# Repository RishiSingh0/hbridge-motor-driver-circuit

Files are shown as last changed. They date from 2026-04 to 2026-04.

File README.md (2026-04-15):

# H-Bridge Motor Driver

This is the motor driver for **Robo Maestro**, a piano-playing robot I built with my team for ELEC 391 (2025W2). It lives on its own daughter board and drives a geared DC motor that slides the robot's hand left and right along the keyboard. A PID loop running on an STM32F446 on the [piano-robot-motherboard](https://github.com/RishiSingh0/piano-robot-motherboard) closes the position loop over this board.

The short version: I designed it, it passed the half-way demo on a bench DC signal, and the first time the control team hit it with real PWM at 10 kHz the MOSFETs started cooking within seconds. The boards were already fabricated, so the fix had to happen on the physical board I already had. The reworked board ran the full song at 20 kHz PWM in the final demo.

---

## The task

My job on the hardware side was an H-bridge the MCU could control to move the robot laterally along the piano. CW would push it right along the keyboard, CCW would push it left, and the PID loop would throw PWM at whichever direction pin it wanted active.

## The board I designed

The design split the MCU side from the motor's HV+ rail and used optocouplers to bridge the two. The MCU sat on the low-voltage 3.3 V side and drove the opto LEDs on the CW and CCW lines; the opto outputs on the HV side did the actual gate drive.

Here are the schematic and layout I sent off to JLCPCB:

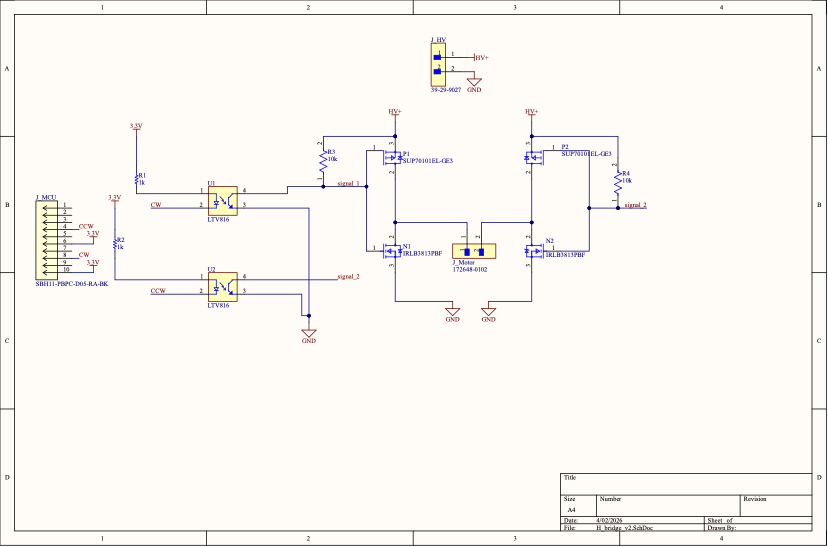
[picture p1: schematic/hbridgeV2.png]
H-Bridge v2 schematic, original as-fabricated design with shared-gate optocoupler drive


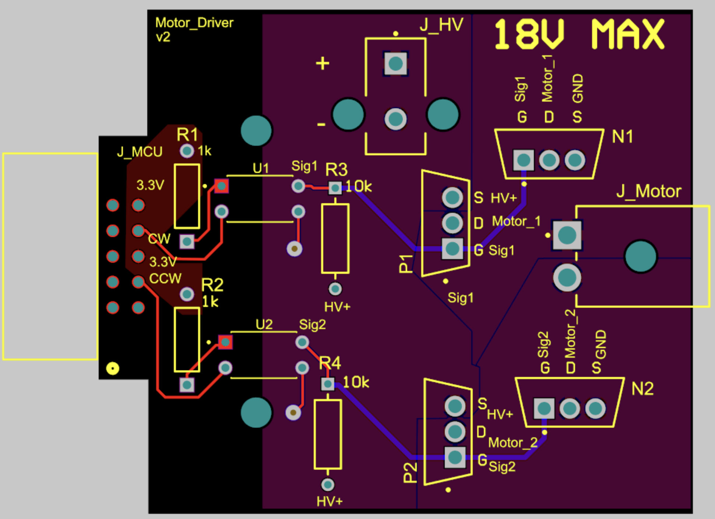
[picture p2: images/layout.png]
H-Bridge v2 PCB layout, top view of the fabricated board with J_MCU connector on the left, the two LTV816 optocouplers driving the gate traces, and two half-bridges feeding the motor connector on the right


One GPIO per leg, through an LTV816 optocoupler, driving **both** the high-side PMOS (SUP70101EL-GE3) and the low-side NMOS (IRLB3813PBF) from the same gate trace. PMOS and NMOS are naturally complementary, so in theory one signal is enough: take the trace high, NMOS on and PMOS off; take it low, PMOS on and NMOS off. Two legs, two opto lines, done. HV+ rail 12–16 V, motor stall 8.5 A, motor connector in the middle.

## The half-way demo passed

For the half-way demo I brought the board up against a bench power supply and tested it the simplest way you can test an H-bridge: hold CW at a 3.3 V DC level on the optocoupler input and watch the motor spin right, then drop CW, assert CCW, and watch it spin left. Motor spun both ways, nothing got hot, and I moved on to integration. (Note: during PID integration the firmware's CW/CCW labels were later swapped, so the final RoboMaestro `MotorCW` drives the opposite physical direction from what this paragraph calls "right".)

A DC command only transitions once, when you change direction, and a single transition is too brief to cause meaningful heating even if shoot-through is happening on it. The bench test was only checking the steady states on either side of the transition, not the transition itself.

## PWM came in during integration and immediately started frying FETs

During integration, the STM32 started driving the H-bridge's CW and CCW inputs with 10 kHz PWM from TIM1 (channels 1 and 2 on PA8 and PA9). Within seconds the MOSFETs started running hot and burning out.

Because the board had worked at the half-way demo, my first instinct was that something on the software side had gone wrong. Nothing in the hardware had changed, and the only new variable was the waveform coming out of the STM32, so I spent a while digging into the firmware (PWM setup, timer channels, the duty cycle path) and got nowhere. Nothing on the software side actually looked broken. In the meantime we dropped the PWM frequency way down just to see what would happen. The FETs still got hot, just much more slowly, which was itself a clue: whatever was cooking them was happening per switching edge, not per steady-state cycle, so it was pointing at something that scaled with transition rate rather than at a software bug.

So I pivoted back to hardware. I searched for why MOSFETs might run hot under PWM and found articles on **shoot-through current** in H-bridges caused by MOSFET transition times. The idea: if both FETs in a half-bridge are even momentarily on at the same time, there's a dead short from HV+ to GND, and if that happens on every PWM edge you're shorting the supply thousands of times a second. I took that to the scope.

## Confirming it on the scope

I put a Tektronix scope on one half-bridge leg and looked at VGS on both FETs simultaneously:

- Low-side (NMOS): probe directly on the gate, since the source is at GND.
- High-side (PMOS): math channel `CH1 − CH2`, with CH1 on the PMOS gate and CH2 on its source at HV+. You need the difference because the PMOS source floats at HV+, not GND.

Then I fed PWM in and froze the scope on a transition edge:

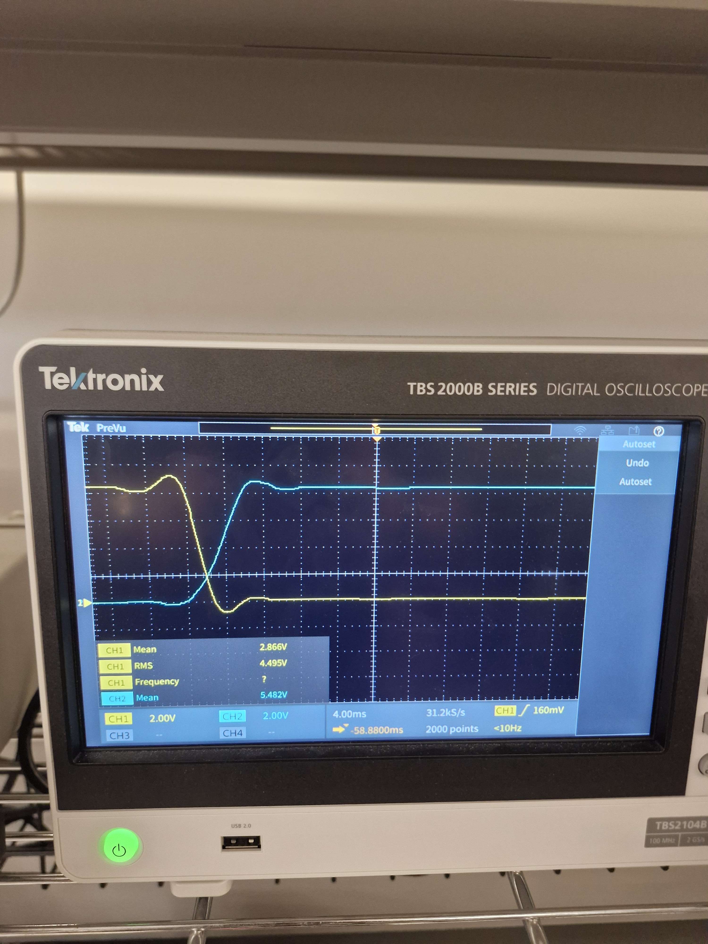
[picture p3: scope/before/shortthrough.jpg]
Scope trace before the rework: both VGS traces transition at the same instant and cross through the mid-rail together, with an X-shaped overlap region where both FETs are partially conducting


Both traces X through each other in the middle of every edge. For the duration of that X, both FETs are sitting in their linear regions together and there's a low-resistance path from HV+ through both of them straight to GND. At 10 kHz that's happening on every single PWM edge, which works out to tens of thousands of near-shorts across the supply per second. Exactly what was cooking the FETs.

## Where the slow transition actually comes from

With the failure confirmed on the scope, I went back to the datasheets to work out why the transitions were so slow in the first place.

The LTV816 phototransistor output transition time alone is around 4 µs typical and up to 18 µs worst case. That's already a long edge. On top of that, the shared-gate node on each leg is loaded by both the PMOS and the NMOS input capacitance (Ciss), which for these power FETs is in the multi-nF range each. Call it somewhere around 10–15 nF total hanging off the 10 kΩ pull-up.

That gives an RC time constant somewhere around 100–150 µs, comparable to or longer than the 100 µs PWM period at 10 kHz. The gate can't finish its transition before the next one starts, so both FETs spend a huge fraction of every period sitting in their linear region at the same time. With these parts and this topology, there was no PWM duty cycle that would have actually worked at 10 kHz.

## The constraint I had to design around

The boards were already fabricated and populated. Whatever the fix was, it had to happen on this physical piece of FR4, not a respin.

## The idea I considered and dropped

My first instinct was to add some form of dead-time: either on the firmware side, or with passive components at the gates. I spent a bit of time on this before realising that if I could just give the MCU direct hardware control over when each PMOS is allowed to be on, I wouldn't need dead-time in the first place. The PMOS could only ever be on when the firmware explicitly said so, and the firmware would simply never allow both PMOSes on at once. Software dead-time also had a separate problem: it would have inserted delay into every PWM transition, which would have shown up as tempo drift in the piano playing since the PID is closing a position loop around a moving musical instrument. The hardware enable approach avoids both issues, and that's the direction I went.

## The fix: break the shared gate and give the MCU hardware enables

Instead of trying to shape the existing shared-gate drive, I decided to split it apart and give the MCU **independent** control of each PMOS. Here's the clean schematic of the post-rework topology:

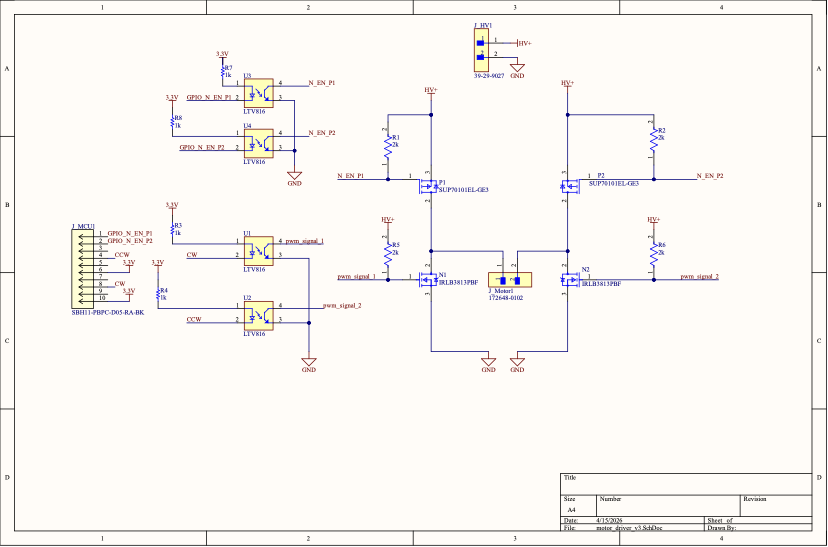
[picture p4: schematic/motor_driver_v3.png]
v3 schematic of the reworked H-bridge: original LTV816 optocouplers (U1, U2) driving only the NMOS gates through 2 kΩ pull-ups, plus two new LTV816 optocouplers (U3, U4) driven by dedicated GPIO enable signals and driving the PMOS gates through their own 2 kΩ pull-ups


And the handwritten planning sketch from when I was deciding what to cut and where to jump:

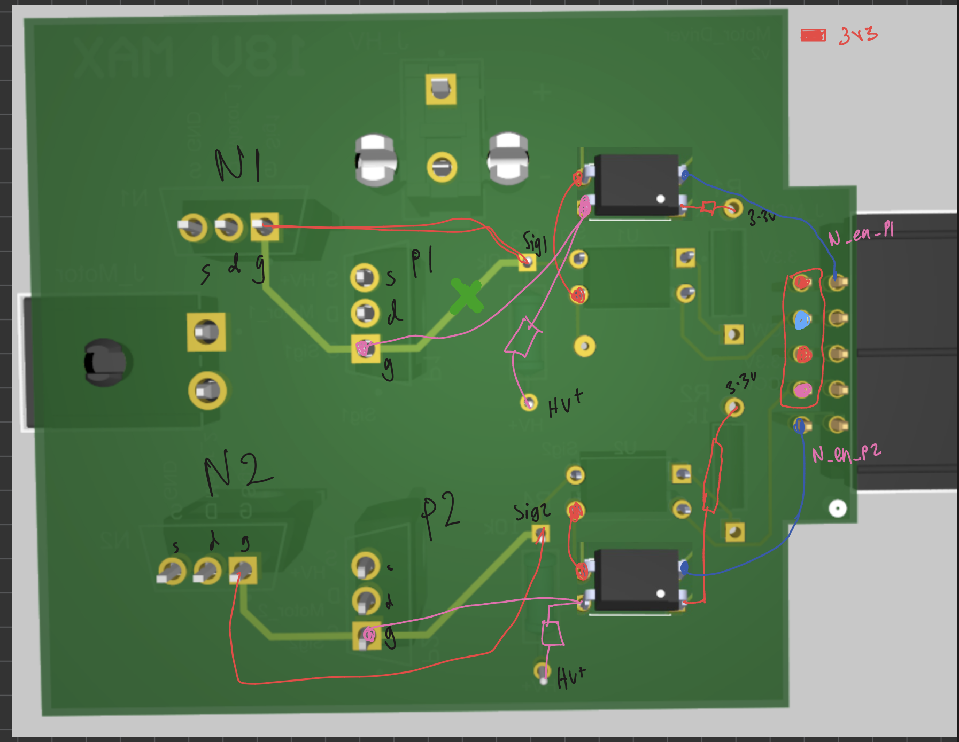
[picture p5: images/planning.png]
Handwritten planning sketch for the rework, showing which traces to cut and where to route the new enable signals


The new topology:

1. Cut 4 traces, two per leg (one on the gate-to-gate run between the NMOS and PMOS, one on the signal trace going into the PMOS gate). In hindsight one cut per leg would have been enough, just the signal-to-PMOS-gate trace, and the original front-side optocoupler could have kept driving the NMOS while the new back-side optos drove the isolated PMOS gates. But I did this rework between 1 and 4am and wasn't optimising for minimum cuts; I just wanted the PMOS gate completely off the shared node.
2. Desolder the original 10 kΩ pull-ups (R3, R4) and replace them with 2 kΩ. These resistors sit on the (now NMOS-only) shared node, and the smaller value drops the RC time constant enough for the NMOS gate to track 10+ kHz PWM without the transition-overlap problem.
3. Add 2 new STM32 GPIOs (PB5 and PB6) as dedicated PMOS enables, one per leg.
4. Add 2 new single-channel optocouplers driven by those GPIOs, wired to the now-isolated PMOS gates. Also solder in 2 more 2 kΩ resistors as pull-ups on the new optos' output side so the PMOS gates have a defined state when the enable signal is idle.

The two new optos were soldered **directly onto the back of the existing PCB**. The original LTV816s were through-hole parts, so their pins were already exposed on the back side and I could tap into them with bodge wires. No extra perfboard, no sub-board, just two optos and some wire on the back of the existing board.

Here's what the rework looked like from behind:

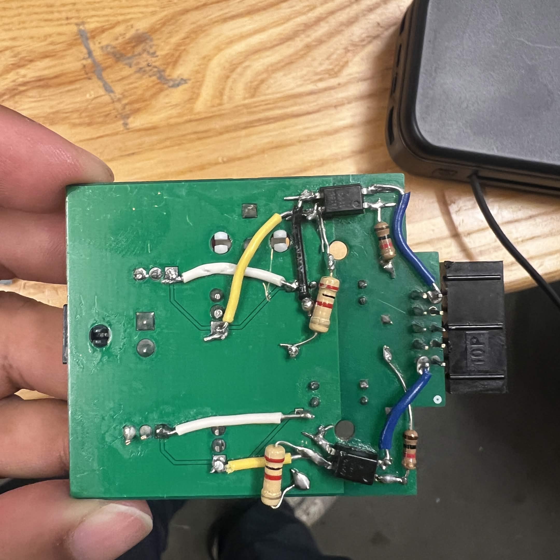
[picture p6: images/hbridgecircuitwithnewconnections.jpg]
Back side of the H-bridge PCB with two single-channel optocouplers and bodge wires soldered on, implementing the enable-signal rework


And the new enable signal lines being tapped into on the motherboard side:

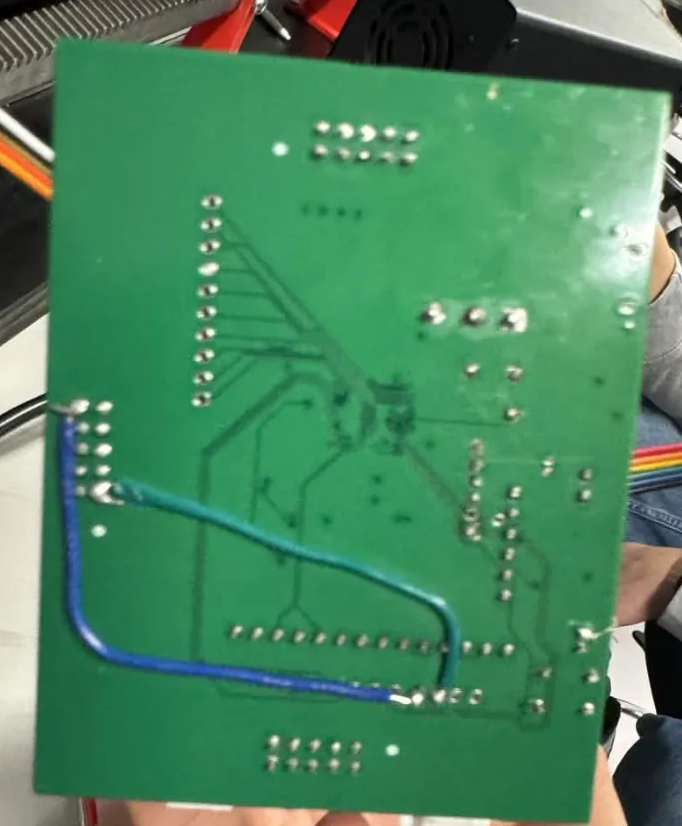
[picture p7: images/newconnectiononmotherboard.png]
New enable signal wires soldered onto the back of the motherboard, connecting two STM32 GPIOs out to the H-bridge daughter board's added optocouplers


And reinstalled in the stack:

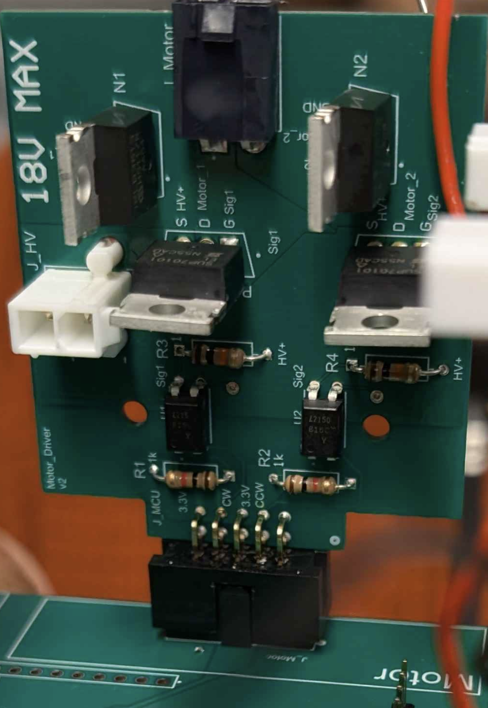
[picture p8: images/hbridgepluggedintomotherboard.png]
Reworked H-bridge daughter board plugged back into the motherboard stack


After the rework, the total signal count into the H-bridge was 4 GPIOs: 2 PWM lines to the NMOSes (unchanged from the original), plus 2 enable lines to the new PMOS-drive optos. The firmware-side logic, written in terms of the actual MCU pin voltages, collapses into a small table:

| State | EN1 | EN2 | N1 | N2 |
|---|---|---|---|---|
| Idle / coast | 3.3V | 3.3V | 0V | 0V |
| Drive CW | 0V | 3.3V | 0V | PWM |
| Drive CCW | 3.3V | 0V | PWM | 0V |

`EN1`/`EN2` are **active-low** through the opto (0V → LED lit → BJT on → PMOS gate pulled low → P ON). `N1`/`N2` are **non-inverting** overall (3.3V → N ON, 0V → N OFF), so "PWM" in the table means the pin is pulsed between 0V and 3.3V and the NMOS follows directly. CW drives diagonally through P1 + N2; CCW drives diagonally through P2 + N1.

On any CW↔CCW transition, the firmware first drives both EN pins to 3.3V (both PMOSes off) before asserting the opposite pair. No overlap is possible, because the PMOSes can only be ON when the MCU explicitly pulls an EN pin low, and the firmware never pulls both EN pins low simultaneously.

The two new optos don't need to be fast either. They're not in the PWM path. They only switch at direction changes, which happen orders of magnitude slower than the PWM frequency, so their multi-µs transition times don't matter.

## After the rework

Back on the scope, same probe setup as before:

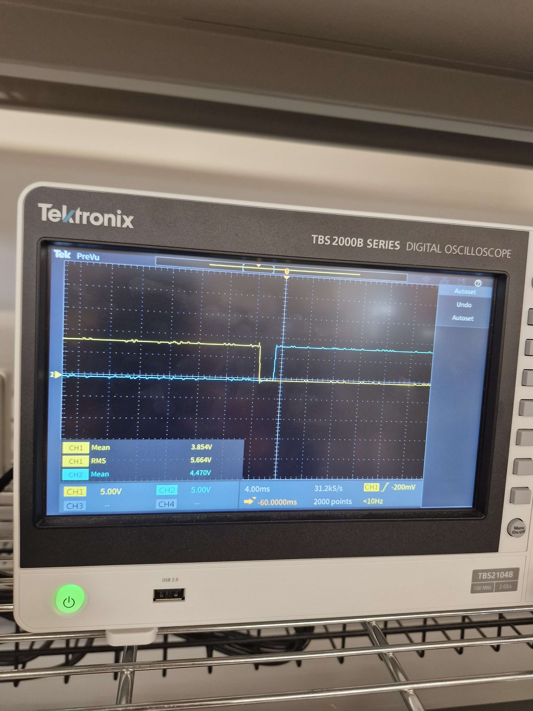
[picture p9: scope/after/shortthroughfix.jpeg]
Scope trace after the rework: one VGS goes fully to its off state before the other asserts on, with a clear horizontal gap between the two edges


Clean non-overlap. One FET is fully off before the other turns on, and there's a clear horizontal gap where neither FET is conducting. No overlap, no shoot-through, no low-resistance path. Same behaviour on both the rising and the falling edge of the switching cycle.

I brought the PWM back up to 10 kHz, then pushed it to **20 kHz for the final demo performance**. The FETs stayed cool at both frequencies, and the robot played the full song end-to-end on the reworked board.

## What I'd do differently

1. **PWM has to be in the very first integration test.** Shoot-through only shows up during a transition, so a DC bench bring-up is structurally incapable of catching it. If you wait until PID integration to introduce PWM, the first time you see the failure is also the first time you're losing FETs.
2. **Don't roll complementary MOSFET drive from a generic optocoupler.** LTV816 transition times (up to 18 µs) are more than an order of magnitude slower than the sub-microsecond edges you need at 10–20 kHz. If I respin this board, I'm using a dedicated half-bridge gate driver IC (IR2184 / IR2110 or similar) with built-in dead-time, or driving each gate independently from the start and adding firmware dead-time explicitly.

---

## Files in this repo

- [`schematic/hbridgeV2.pdf`](schematic/hbridgeV2.pdf): the as-fabricated v2 schematic shown at the top of this README (rendered PNG next to the PDF)
- [`schematic/motor_driver_v3.pdf`](schematic/motor_driver_v3.pdf): the post-rework v3 schematic shown in the fix section (rendered PNG next to the PDF)
- [`hardware/`](hardware): Altium source for the fabricated v2 design (schematic, PCB, BOM, project file)
- [`scope/before/`](scope/before) and [`scope/after/`](scope/after): scope captures of VGS on one half-bridge leg before and after the rework
- [`images/`](images): planning sketch, original PCB layout, and photos of the bodged board
- [`notes.txt`](notes.txt): the raw notes I wrote while figuring out the fix, preserved as-is

There's no v3 PCB layout planned; the final demo ran on the reworked v2.

## Related

- Main system repo: [piano-robot-motherboard](https://github.com/RishiSingh0/piano-robot-motherboard)
- Background reading that helped: [AllAboutCircuits: H-bridge dead-time and shoot-through](https://www.allaboutcircuits.com/technical-articles/h-bridge-dc-motor-control-complementary-pulse-width-modulation-pwm-shoot-through-dead-time-pwm/)

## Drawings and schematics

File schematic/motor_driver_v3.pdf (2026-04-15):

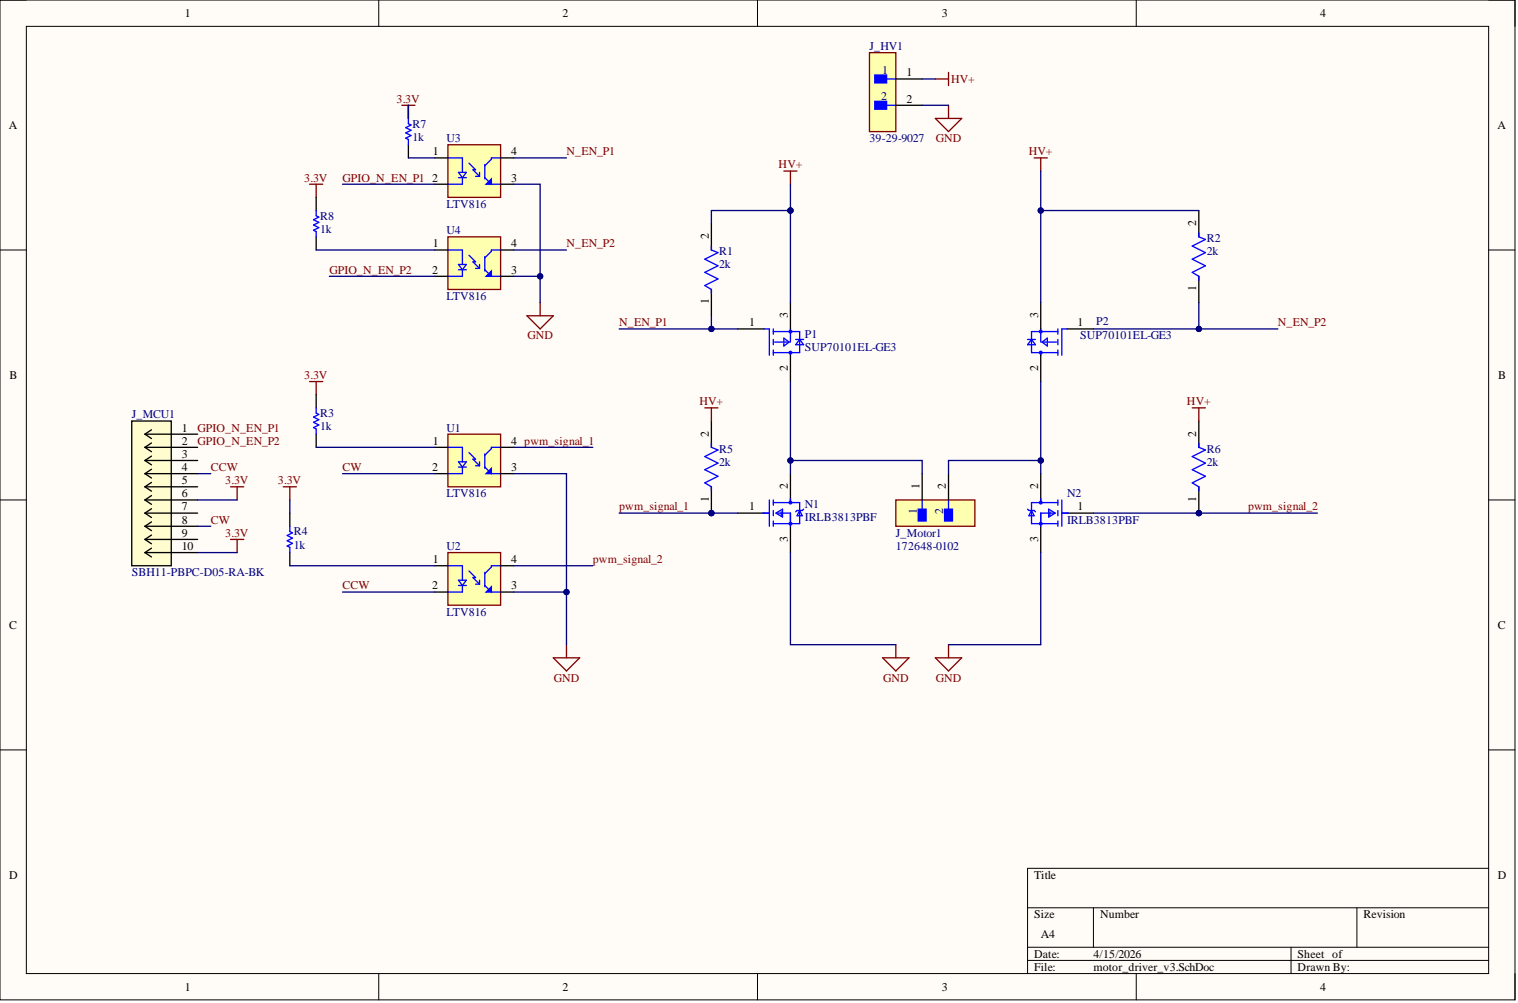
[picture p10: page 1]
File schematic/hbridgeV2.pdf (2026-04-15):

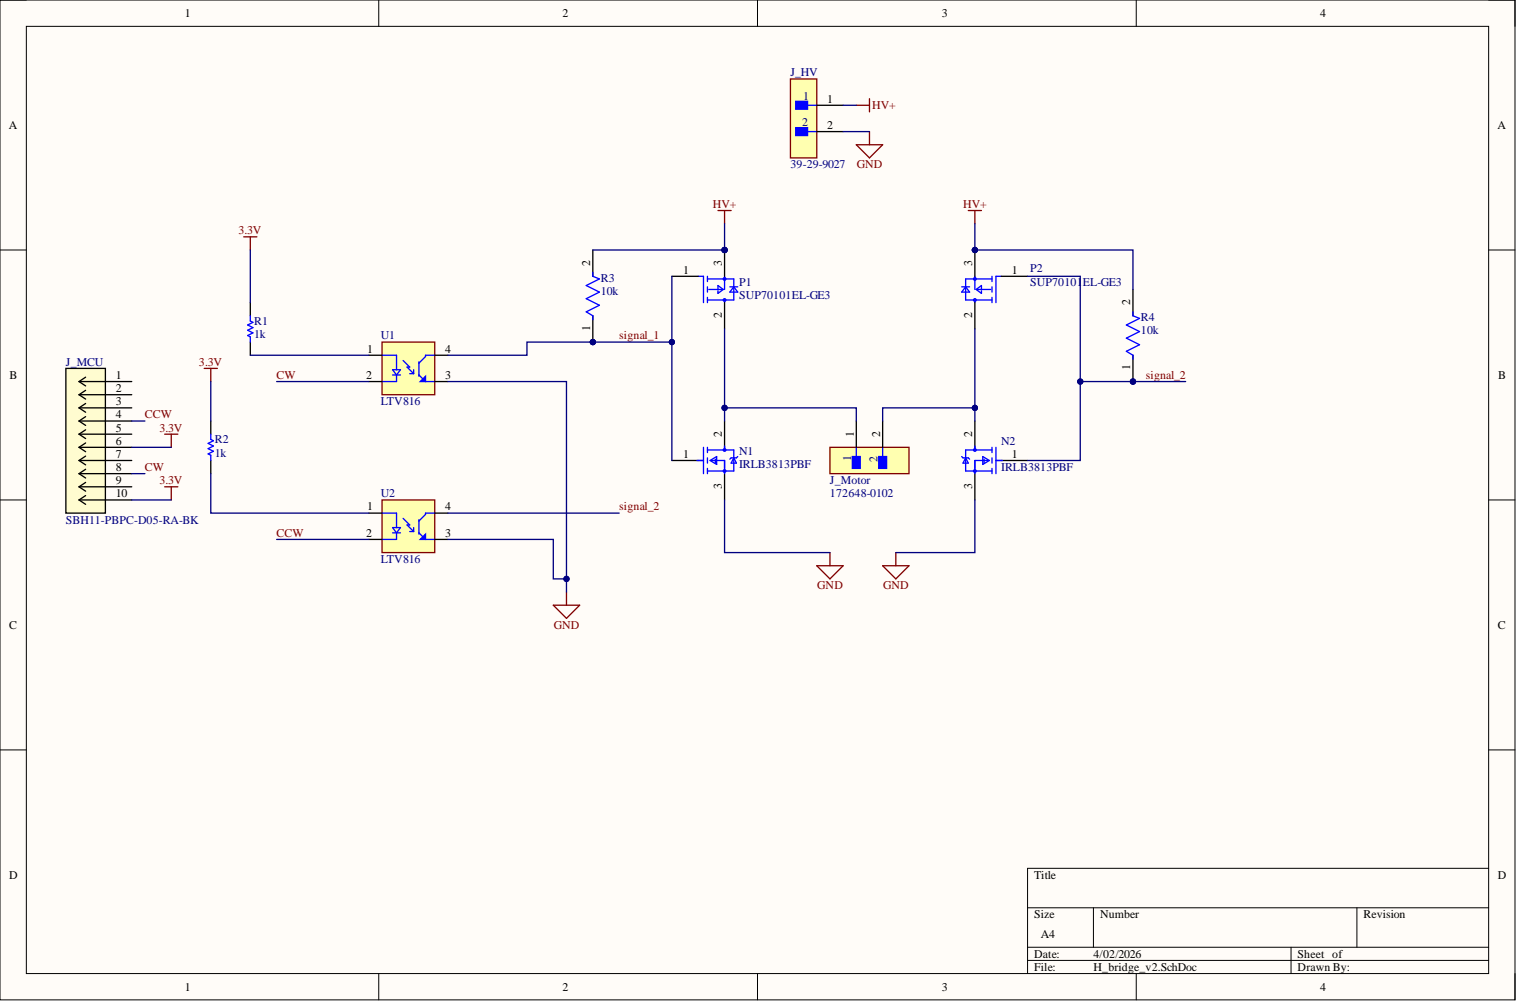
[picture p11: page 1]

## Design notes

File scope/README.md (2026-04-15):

# Oscilloscope Captures

Probe setup for measuring shoot-through on one half-bridge leg:

- **Low-side VGS (N-channel):** probe gate directly, source is GND.
- **High-side VGS (P-channel):** scope math channel `CH1 - CH2`, with CH1 on the PMOS gate and CH2 on the PMOS source (HV+).

If both VGS traces show the FETs in their ON region at the same time during a PWM edge, shoot-through is confirmed.

- [`before/shortthrough.jpg`](before/shortthrough.jpg): original board under PWM. Both VGS traces cross through the linear region at the same time on each edge; the X-shaped overlap is the shoot-through window.
- [`after/shortthroughfix.jpeg`](after/shortthroughfix.jpeg): same probe points after the rework. One VGS is fully off before the other turns on, with a clear non-overlap gap between edges. Verified on both rising and falling transitions of the switching cycle.

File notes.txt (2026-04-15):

Original notes written while planning the rework (preserved verbatim):

Hbridge circuit was causing short through current the mosfet was too slow to switch off one one side when hit with pwm when tested with bench power supply it was fine as it was straight dc signal but when hit with pwm the switching resulted in the mosfet falling and rise time to match multiple times leading to vdd and gnd shorting resulting in current flow and heating up of the mosfets eventually frying them. PCBs were already ordered so needed to implement a solution on thhe current pcb cut 4 traces and added 2 new gpio connections as enable signals. Resulting in dead time being added on software side. Attached two new single channel optocoupler and soldered new connections on the back of the pcb resulting in 4 total gpis.

this should eliminate the switching of the pmos that we got from the original schematic when one half is conducting current
and when switching from CW -> CCW, all PMOS's turn off first and then switch
ill breadboard it tmrw and maybe we can test it
to implement it on our pcb we need to:
cut the gate traces to the pmos
solder on two optos onto a perfboard
add the pull down resistors on the nmos

Wait we dont need deadtime nvm if we have hardware solution. Come up with the logic table as wel for these new connections.

https://www.allaboutcircuits.com/technical-articles/h-bridge-dc-motor-control-complementary-pulse-width-modulation-pwm-shoot-through-dead-time-pwm/

So I believe I implanted a hardware solution instead of dead time which is on firmware side? It would cause more delay?
